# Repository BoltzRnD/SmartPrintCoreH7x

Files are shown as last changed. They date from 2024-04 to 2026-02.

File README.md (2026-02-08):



        The SmartPrintCoreH7x is an open-source 3D printer mainboard based on the STM32H7 series microcontroller.
        Copyright (C) 2024 Boltz R&D

        This Project is free Hardware: you can redistribute it and/or modify
        it under the terms of the GNU General Public License as published by
        the Free Software Foundation, either version 3 of the License, or
        (at your option) any later version.

        This Hardware is distributed in the hope that it will be useful,
        but WITHOUT ANY WARRANTY; without even the implied warranty of
        MERCHANTABILITY or FITNESS FOR A PARTICULAR PURPOSE.  See the
        GNU General Public License for more details.

        You should have received a copy of the GNU General Public License
        along with this program.  If not, see <https://www.gnu.org/licenses/>.

Contact - info@boltzrnd.com

# Contribute
I am looking for contributors and Open source organisations to maintain, expand and customize the design and sources for a voron 2.4 or similar next gen machines. being stuck in other work get me little to no time to make this project go forward for open source.

# SmartPrintCoreH7x
### Now Available to Buy from <a href="https://boltzrnd.com">Boltz R&D Store</a> , We are Shipping Globally!

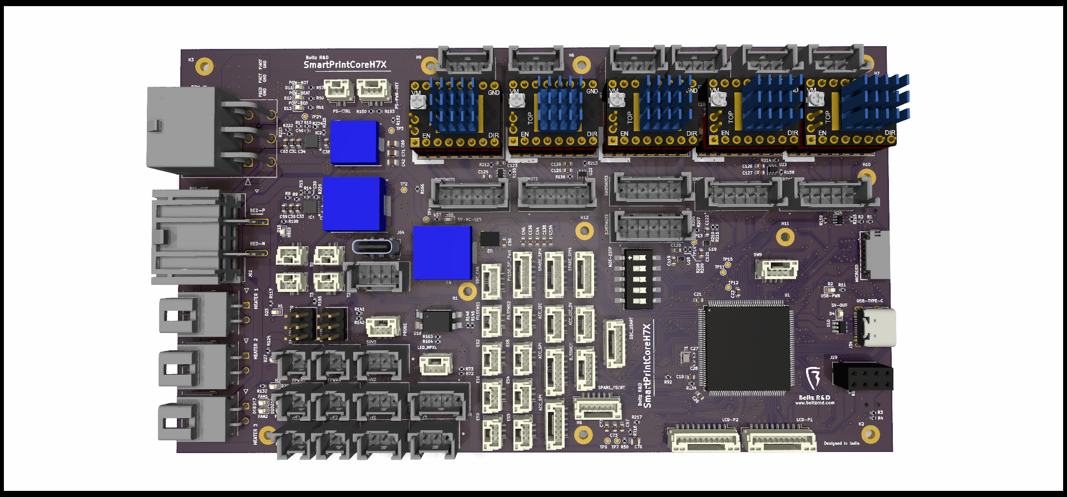
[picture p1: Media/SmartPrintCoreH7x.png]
SmartPrintCoreH7x


SmartPrintCoreH7X © 2024 by Boltz R&D is licensed under GPL V3. To view a copy of this license, visit https://www.gnu.org/licenses/gpl-3.0.en.html ---------------

The SmartPrintCoreH7x is an open-source 3D printer mainboard based on the STM32H7 series microcontroller. It includes 5+1 stepper drivers, with the option to expand by adding more sets of 5 drivers through the upcoming "SmartPrintCore Extravaganza". With a jumper-less setup and a design built for flexibility, SmartPrintCoreH7x is dedicated for makers, tinkerers, and the industry to build and customize.

The Board utilizes self-locking Molex MegaFit(Power Input), Ultra-Fit Tangless (Hotend Heaters), Mini-Lock(Motors and power peripherals) and JST-GH (Digital and IO Peripherals), for easy and worry-free connections.

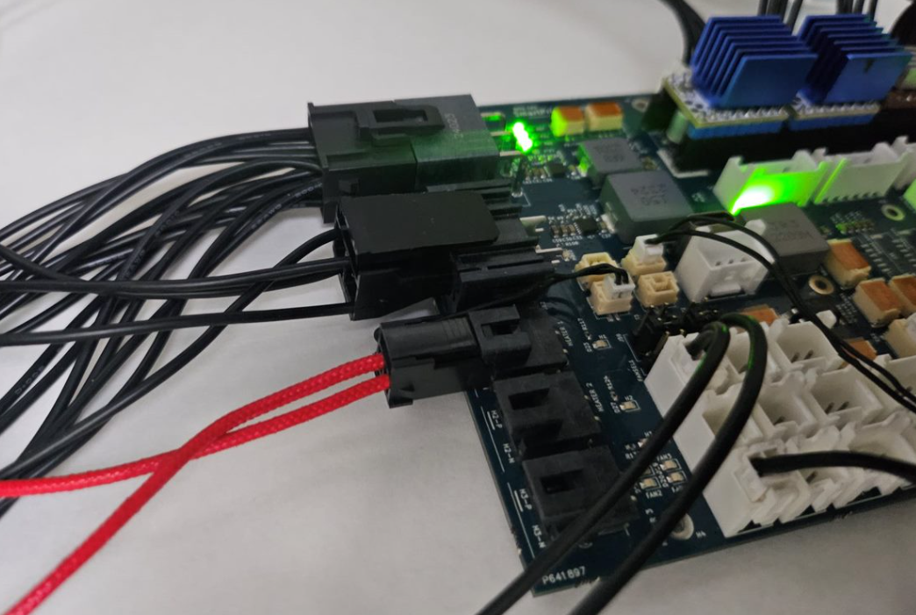
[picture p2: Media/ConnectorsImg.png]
Self-Locking Connectors Self-Locking Connectors in Action

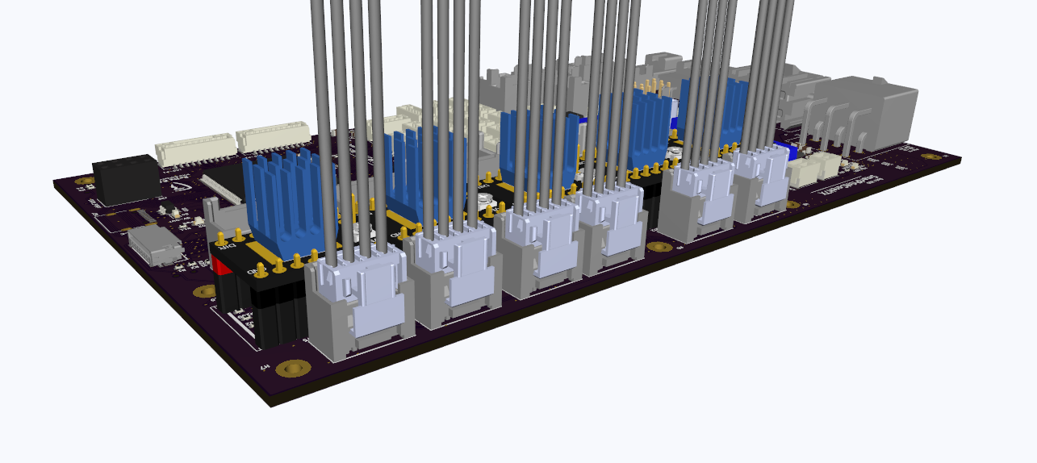
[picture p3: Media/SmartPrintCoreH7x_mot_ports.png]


The board also includes multiple TI Buck converters with more than 90% efficiencies for multiple peripherals
1. 12V 5A Fan and Peripheral Supply
2. 5V 5A Fan and Peripheral supply
3. 5V 10A SBC Supply (Optional, Can be powered by Peripheral Supply, using resistor jumpers in production)

Other notable features include -
1. Compatibility with 12V/24V power supplies
2. Auto power source selection for Board supply from USB/Main Supply.

Theraml Considerations - 
1. Low RDS(on) Mosfets are used for minimal losses, which also allows heatsink-less operation for average use cases
2. The PCB design prioritizes heat management, with strategically placed components and optimized power traces that ensure optimal cooling.

## All Features

1. Open-source design, accessible and modifiable.
2. Developed in KiCad.
3. Powered by STM32H723 MCU.
4. Supports 5+1 Stepper motors (Expandable in multiples of 5 using SmartPrintCore Extravaganza expansion board).
5. Supports dedicated five closed-loop external stepper ports.
6. USB-C with auto power switching for seamless MCU power management without setting jumpers.
10. Four PWM and two always-on fan ports (Total 6 Fan ports).
11. Dual voltage compatibility with 24V and 12V power supplies.
12. Four servo channels.
13. Single side-entry locking connector for simplified power input.
14. TI buck converters ensure efficient and reliable power supply to SBC and components.
15. Dedicated 5V supply for SBC (10A max, to support Bigger LCD and other SBC peripherals) with locking connector and Type-C port.
16. Auxiliary power: 5V 5A and 12V 5A for peripherals and fans.
17. 3.3V 1A auxiliary supply for Wi-Fi modules and small devices.
18. High-efficiency MOSFETs for cooler operation.
19. 15A heated bed with a locking connector.
20. Three high-power heaters with locking connectors.
22. Onboard slow-burning fuse for added safety.
    - Optional: External additional inline fuses for power input are recommended (included in BOM).
24. DIP switch configuration for easy sensorless homing setup.
25. Preconfigured switchable microstepping with preinstalled SMD resistors.
26. Buffered signals for motor SPI and UART.
27. Supports both Marlin and Klipper firmware.
28. Clearly marked stepper drivers for easy orientation identification and setup.

## Ports Overview

| Port Category | Quantity | Details |Recommended Rating(Operating) | Current Rating (Absolute Max Unless Notified)|
|---|---|---|---|---|
| Power Input | 1 | 6-in-1; Min: 12V, Max - 24V | 15A | 60A Total: 20A BED, 20A Motors, 20A Heaters  |
| Steppers | 5 (+1) | 2 Ports for Z Stepper | 15A | 20A |
| Smart Steppers Port | 5 (+1) | | 15A | 20A |
| Heaters | 3 | | 15A | 20A |
| Bed Heaters | 1 | | 15A | 20A |
| Accelerometer | 3 (Total) | 1 x SPI 3.3V, 1 x I2C 5V, 1 x I2C 3.3V | 0.5A | 1A |
| ESP-01 UART | 1 | | 0.5A | 1A |
| FAN | 6 | 4 x PWM + 2 x Always On, Switchable | 2A each port,4A across all ports | 5A |
| Servo | 4 | | 2A each port,4A across all ports | 5A |
| Aux Servo Power | 1 | 5V | 4A | 5A |
| SPI (Spare) | 3 | 1 x 3.3V + 2 x 5V | 0.5A | 1A 5V, 0.2A 3.3V |
| PT100 SPI Port | 1 | | 0.2A | 0.2A |
| USART | 2 | | 1A | 2A |
| SBC Supply | 2 | 1 x 4-pin Connector + 1 x Type C | 8A | 10A |
| CAN | 1 | | 0A(No Power on CAN Port) | 0A |
| Temperature Sensors | 4 | | N/A | N/A |
| Endstops | 6 | | N/A | N/A |
| Filament Sensors | 2 | | N/A | N/A |
| LCD Connector Set | 1 | | 1A | 2A |
| SWD | 1 | | N/A | N/A |
| PS CTRL | 1 | | N/A | N/A |
| PS PWR DET | 1 | | N/A | N/A |
| Neopixel LED Port | 1 | | 1A | 2A |
| BLTOUCH Port | 1 | | 1A | 2A |
| Probe | 1 | | 1A | 2A |
| MicroSD | 1 | | N/A | N/A |

## Jumpers and Configurations

| Configuration | Options | Description |
|---|---|---|
| Sensorless Homing | 1 | Configurable through onboard DIP switches |
| Fan Voltage Selection | 2 | Selectable voltages: 12V, 5V, or POWER_IN |

## Design Considerations
To optimize general usage and simplify installation, the following design features have been incorporated:

1. **External Inline Fuses**: Installed beyond the power supply line for easy fuse replacement without the need to dismantle the mainboard section of your printer.
2. **Pre-Configured Stepper Jumpers**:
   - Jumpers are preset to high using 0402 resistors, eliminating the need for manual adjustments.
   - MSX bit changes are managed via firmware if you are utilizing hardware settings.
   - Note: A4988/DRV8266 and SPI-based drivers cannot be mixed and used concurrently without soldering additional 0402 configuration resistors.

## Contribute to the SmartPrintCore Open Source Project Lineups

We are actively looking for contributors to keep this project alive, Join us in making 3D printing more accessible, reliable, and fun for everyone. Let's create, innovate, and inspire the future, one layer at a time.

Feature Requests and Bug Reports are most welcome :)

## Buy From
1. Boltz R&D - Contact us at info@boltzrnd.com or Buy Directly from https://www.boltzrnd.com
2. -- More to Come --

Interested in becoming a listed manufacturer? Reach out to us at info@boltzrnd.com to add your store link here.

## Compatible Accesories -
1. Cases -
Note - Stay tuned to our Thingiverse channel to be the first one to know - https://www.thingiverse.com/boltzrnd/designs

# Story Time

### How It Was Created
SmartPrintCoreH7x was born out of a combination of long commute hours and a renewed passion for building. With 7 hours a day of travel time, a result of embarking on an exciting single life, there was a great opportunity to reconnect with my hobby of creating innovative hardware. Fueled by endless cups of Chai Tea and free time, I found a new rhythm between the rails and circuits.

### Why It Was Created
The motivation behind SmartPrintCoreH7x is rooted in both personal need and a broader vision for the 3D printing community:
- **High-Speed Performance**: Designed to handle extremely high printing speeds of 300 mm/s or more.
- **Unmatched Control**: Providing complete control over the hardware, allowing for extensive customization and modification at any time to meet evolving needs, for any organization and individuals.
- **Reliable and Easy Connections**: To eliminate common issues with connectivity in intensive printing operations.
- **Open Source Commitment**: Ensuring the hardware remains open and accessible, allowing anyone to modify and improve upon the design without restriction.
- **Safety and Reliability**: Integrating robust power supplies to safeguard the system, particularly enhancing the performance and reliability of connected Single Board Computers (SBCs).

# Commitment to Open Source

**Note:** In celebration of our dedication to open-source hardware and software, Boltz R&D endorses the use of BeaglePlay and BeagleBone SBCs with SmartPrintCoreH7X. We are committed to actively supporting the community by ensuring seamless interfacing and integration of these setups or similar setups.

# Extra notes

1. Marlin Configuration is still under development, Please Raise a requirement on discord to prioritize it above other tasks if needed.
2. The Component Libraries are not included and redistributed because of license restrictions, contact us to join our organisation as a "contributor" to access the part libraries for development.
3. Custom 3D Printed casing is under development and evaluation, and is expected to release by end of May 2024.
4. The Klipper Configuration files are minimal, and will require some modifications to fit your use case, reach out to us whenever in doubt.
5. Feel Free to reach out to our discord server for any queries related to integration, development and production.
6. You can also send us feature requests that you'd like to see in the next versions of the board.

# Disclaimer

The SmartPrintCoreH7x is an open-source project provided by Boltz R&D. It is offered "as is" and without any warranties or guarantees, express or implied.

Boltz R&D provides no warranty of any kind regarding the safety, reliability, durability, and performance of the SmartPrintCoreH7x. By using this project's design, software, or hardware, you expressly acknowledge and agree that you assume all risks associated with its use.

Boltz R&D shall not be liable for any claims, damages, or other liabilities whatsoever, whether in an action of contract, tort or otherwise, arising from, out of, or in connection with the SmartPrintCoreH7x or the use or other dealings in this project.

This project is provided as an open-source resource for the community to use, modify, and distribute subject to the terms of the GPL V3 license. All third parties manufacturing, selling, or using the SmartPrintCoreH7x are responsible for ensuring that their products and services comply with all applicable laws and regulations.

Users are responsible for compliance with local laws, and for ensuring that appropriate safety measures are in place when manufacturing, using, or modifying the SmartPrintCoreH7x mainboard.

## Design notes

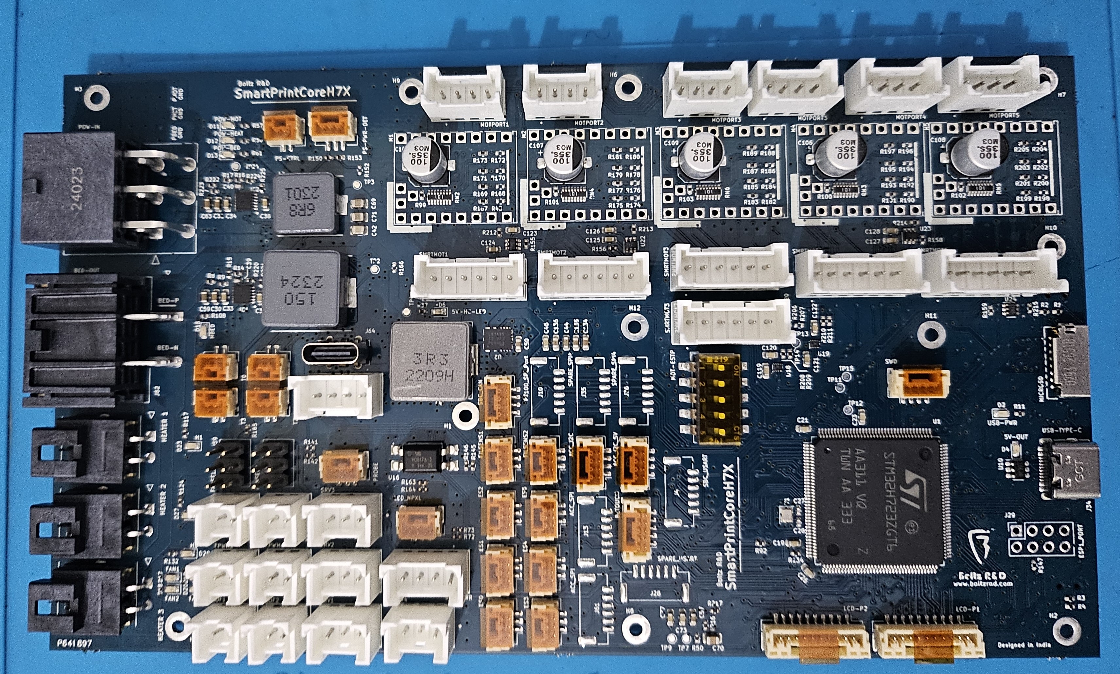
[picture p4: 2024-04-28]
Media/TheProto.jpg

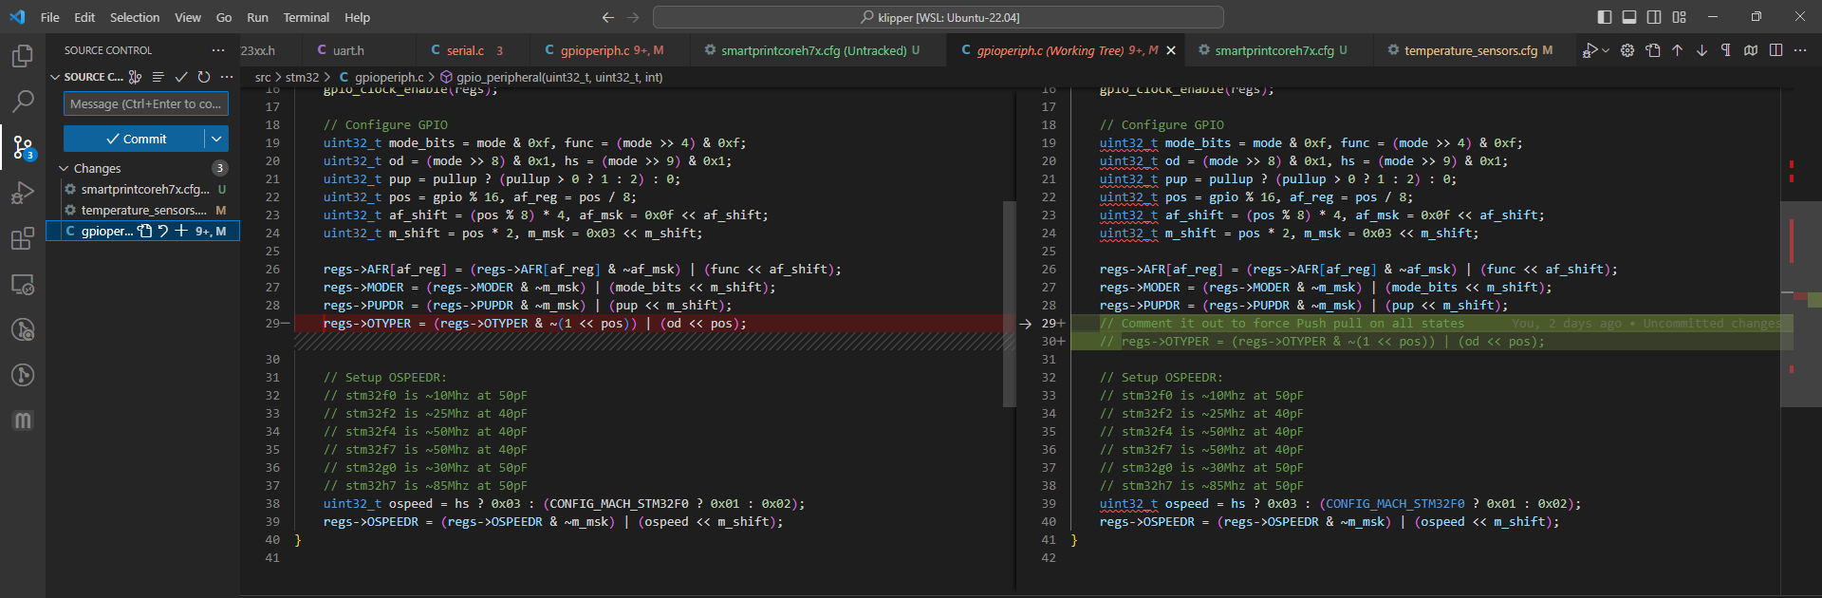
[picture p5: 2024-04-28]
FirmwareConfigs/PushPull_serial.png

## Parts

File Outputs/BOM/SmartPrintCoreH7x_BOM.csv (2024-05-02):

Reference | Value | Footprint | Manufacturer_Part_Number | Qty
C1, C3, C5, C10-C13, C15-C26, C29, C33-C35, C37, C38, C43, C45-C49, C51, C52, C58, C62, C65, C72-C83, C85, C87-C92, C94-C96, C98, C99, C101, C103, C110, C111, C115, C119-C130, C137 | 100nF | Capacitor_SMD:C_0603_1608Metric | CL10B104JB8NNNC | 78
C2, C7-C9, C14, C84, C93, C100, C102, C104 | 2.2uF | Capacitor_SMD:C_0603_1608Metric | GRM188R61E225KA12J | 10
C4, C6, C32, C36, C50, C57, C86, C116, C135, C136 | -- mixed values -- | Capacitor_SMD:C_0603_1608Metric | CL10A105KB8NNNC | 10
C27, C28 | 6pF 1% | Capacitor_SMD:C_0402_1005Metric | GCM1555C1H6R0FA16D | 2
C30, C31, C44, C59, C63, C64, C134 | 10uF 50V | Capacitor_SMD:C_0805_2012Metric | GRM21BR61H106KE43L | 7
C39, C40 | 1pF 50V | Capacitor_SMD:C_0402_1005Metric | CC0402CRNPO9BN1R0 | 2
C41, C60, C61, C66, C114 | 22uF 35V | Capacitor_SMD:C_1206_3216Metric | C3216X5R1V226M160AC | 5
C42, C69, C71, C117, C118 | 47uF 10V | Capacitor_SMD:C_0805_2012Metric | GRM21BR61A476ME15L | 5
C53-C55 | 100uF 10V | Capacitor_SMD:C_1210_3225Metric | GRM32ER61A107ME20L | 3
C56, C139-C153 | 10uF 50V | Capacitor_SMD:C_1206_3216Metric | CL31A106KBHNNNE | 16
C67, C68, C70, C97, C112 | 10uF 16V | Capacitor_SMD:C_0805_2012Metric | CL21A106KOQNNNE | 5
C105-C109 | 100uF 35V | Capacitor_SMD:CP_Elec_6.3x7.7 | EEE-1VA101XP | 5
C113 | 4.7uF | Capacitor_SMD:C_0603_1608Metric | C1608X7S1A475K080AC | 1
C131-C133 | 2.2uF 100V | Capacitor_SMD:C_1210_3225Metric | CL32B225KCJSNNE | 3
C138 | 12pF | Capacitor_SMD:C_0402_1005Metric | GRM1555C1H120GA01D | 1
D1 | CDSOT23-T24CAN | CDSOT23-T24CAN:SOT95P230X117-3N | CDSOT23-T24CAN | 1
D2, D3 | -- mixed values -- | LED_SMD:LED_0603_1608Metric | B1911UYG-20D000114U1930 | 2
D4, D6, D7, D11-D13 | -- mixed values -- | LED_SMD:LED_0603_1608Metric | B1911PG--20D000514U1930 | 6
D8-D10 | SMBJ30C | Diode_SMD:D_SMB | SMBJ30C | 3
D14, D15, D21, D22, D24-D26, D28, D34, D35 | SS14 | Diode_SMD:D_SMA | SS14 | 10
D16-D20, D23, D27, D29 | -- mixed values -- | LED_SMD:LED_0603_1608Metric | B1911UD--20D001014U1930 | 8
D30-D33 | BAV99 | Package_TO_SOT_SMD:SOT-23 | BAV99 | 4
F1-F3 | 20A SLBLW | Fuse:Fuse_1206_3216Metric | SF-1206HH20M-2 | 3
H1-H4, H6-H12, J29, M1-M5, R43, R73, R90, R141, R152, R160, R162, R164, R166, R168, R170, R172, R174, R176, R178, R180, R182, R184, R186, R188, R190, R192, R194, R196, R198, R200, R202, R204, R207, R226, TP1-TP16, TP18-TP25 | -- mixed values -- | -- mixed values -- | DNP/NC | 71
IC1, IC2 | LMR51450SDRRR | LMR51450SDRRR:SON50P300X300X80-13N-D | LMR51450SDRRR | 2
J1 | POW-IN | 0768250006:CON_768250006_MOL | 768250006 | 1
J2, J3, J5, J8, J9 | -- mixed values -- | Connector_JST:JST_GH_BM02B-GHS-TBT_1x02-1MP_P1.25mm_Vertical | BM02B-GHS-TBT | 5
J4, J10, J13, J28, J35, J36, J61 | -- mixed values -- | Connector_JST:JST_GH_BM06B-GHS-TBT_1x06-1MP_P1.25mm_Vertical | BM06B-GHS-TBT | 7
J6, J14, J65 | -- mixed values -- | 172310-3302:1723103102 | 1723103102 | 3
J7, J45, J53-J58 | -- mixed values -- | connectorslibrary:53375-0410 | 53375-0410 | 8
J11, J17, J23, J27 | -- mixed values -- | Connector_JST:JST_GH_BM04B-GHS-TBT_1x04-1MP_P1.25mm_Vertical | BM04B-GHS-TBT | 4
J12, J15, J16, J19, J21, J22, J25, J26, J30, J31, J63 | -- mixed values -- | Connector_JST:JST_GH_BM03B-GHS-TBT_1x03-1MP_P1.25mm_Vertical | BM03B-GHS-TBT | 11
J18, J24 | -- mixed values -- | Connector_JST:JST_GH_BM10B-GHS-TBT_1x10-1MP_P1.25mm_Vertical | BM10B-GHS-TBT | 2
J20 | BLTOUCH | Connector_JST:JST_GH_BM05B-GHS-TBT_1x05-1MP_P1.25mm_Vertical | BM05B-GHS-TBT | 1
J32, J33, J37-J40 | -- mixed values -- | connectorslibrary:53375-0210 | 53375-0210 | 6
J34 | USB_C_Receptacle_USB2.0 | USB_C_MOD:USB_C_Receptacle_XKB_U262-16XN-4BVC11 | USB4105-GF-A | 1
J41-J44 | -- mixed values -- | connectorslibrary:53375-0310 | 53375-0310 | 4
J46 | Micro_SD_Card_Det | microsd:473092651 | 473092651 | 1
J47-J52 | -- mixed values -- | connectorslibrary:53375-0610 | 53375-0610 | 6
J59, J60 | -- mixed values -- | Connector_PinSocket_2.54mm:PinSocket_2x03_P2.54mm_Vertical | PH2-06-UA | 2
J62 | BED-OUT | 1720430206:MOLEX_1720430206 | 1720430206 | 1
J64 | USB_C_Receptacle_PowerOnly_6P | Connector_USB:USB_C_Receptacle_GCT_USB4115-03-C | USB4115-03-C | 1
L2 | 15uH | SRP1265A-150M:INDPM135125X650N | SRP1265A-150M | 1
L3 | 6.8uH | SRP1038CC-6R8M:INDPM110100X400N | SRP1038CC-6R8M | 1
L4 | 3.3uH | SRP1265C-3R3M:IND_SRP1265C-3R3M | SRP1265C-3R3M | 1
L5 | 1uH | Inductor_SMD:L_1008_2520Metric | DFE252012F-1R0M=P2 | 1
Q1, Q3, Q5, Q6 | AO3400A | Package_TO_SOT_SMD:SOT-23-3 | AO3400A | 4
Q2, Q4, Q7, Q8 | TPH3R704PL | TPH3R704PL:TRANS_TPHR8504PL,L1Q | TPH3R704PL | 4
R1, R3 | 220R | Resistor_SMD:R_0402_1005Metric | CRGCQ0402J220R | 2
R2, R4, R6, R7, R45-R47, R50, R55, R64, R67, R70, R75, R77, R80, R83, R85, R87, R92, R99-R104, R106, R113, R115, R118, R120, R122, R125-R129, R131, R133, R144, R147-R151, R154-R159 | 10K | Resistor_SMD:R_0402_1005Metric | CRCW040210K0FKEDC | 50
R5, R72, R134, R142, R161, R163, R165, R167, R169, R171, R173, R175, R177, R179, R181, R183, R185, R187, R189, R191, R193, R195, R197, R199, R201, R203, R205, R206, R216-R219 | 0E | Resistor_SMD:R_0402_1005Metric | CRCW04020000Z0ED | 32
R8 | 2.37M 1% | Resistor_SMD:R_0402_1005Metric | CRCW04022M37FKED | 1
R9, R223 | 200K 1% | Resistor_SMD:R_0402_1005Metric | CRCW0402200KFKEDC | 2
R10, R18-R21, R26-R29, R38-R42, R49, R56, R65, R66, R68, R69, R71, R74, R76, R78, R79, R81, R82, R84, R86, R88, R145, R208-R215 | 120E | Resistor_SMD:R_0402_1005Metric | RC0402FR-07120RL | 39
R11-R13, R37, R48 | 330E | Resistor_SMD:R_0402_1005Metric | CRGCQ0402J330R | 5
R14, R16, R32, R93-R98, R136, R146, R221, R224 | 100K | Resistor_SMD:R_0402_1005Metric | CRGCQ0402J100K | 13
R15 | 7.15K | Resistor_SMD:R_0402_1005Metric | CRCW04027K15FKED | 1
R17 | 19.1K | Resistor_SMD:R_0402_1005Metric | CRCW040219K1FKEDC | 1
R22-R25, R57, R60, R61, R108-R112, R117, R124, R132 | 4.7K | Resistor_SMD:R_0402_1005Metric | CRGCQ0402J4K7 | 15
R30, R35 | 100K 1% | Resistor_SMD:R_0402_1005Metric | CRCW0402100KFKED | 2
R31 | 16.2K 1% | Resistor_SMD:R_0402_1005Metric | CRCW040216K2FKEDC | 1
R33 | 4.99K | Resistor_SMD:R_0402_1005Metric | CRCW04024K99FKEDC | 1
R34, R89 | 5.1K | Resistor_SMD:R_0402_1005Metric | RC0402FR-135K1L | 2
R36 | 24.9K 1% | Resistor_SMD:R_0402_1005Metric | CRCW040224K9FKEDC | 1
R44 | 2.2K | Resistor_SMD:R_0402_1005Metric | CRGCQ0402J2K2 | 1
R51, R52, R58, R59, R63, R137, R138, R140 | 2.37K 1% | Resistor_SMD:R_0402_1005Metric | CRCW04022K37FKED | 8
R53, R54, R62, R139 | 4.7K 0.1% | Resistor_SMD:R_0402_1005Metric | RT0402BRE074K7L | 4
R91, R143 | 1K | Resistor_SMD:R_0402_1005Metric | CRGCQ0402J1K0 | 2
R105, R107, R114, R116, R119, R121, R123, R130 | 12K | Resistor_SMD:R_0402_1005Metric | RC0402FR-1312KL | 8
R135 | 453K | Resistor_SMD:R_0402_1005Metric | CRCW0402453KFKEDC | 1
R153 | 15K 1% | Resistor_SMD:R_0402_1005Metric | RC0402FR-1015KL | 1
R220 | 46.4K | Resistor_SMD:R_0402_1005Metric | ERJ-2RKF4642X | 1
R222 | 1.21M 1% | Resistor_SMD:R_0402_1005Metric | CRCW04021M21FKED | 1
R225 | 37.4K | Resistor_SMD:R_0402_1005Metric | CRCW040237K4FKED | 1
RN1-RN6 | 100E | YC248_JR_07100RL:R_Array_Convex_8x0602 | YC248-JR-07100RL | 6
SW1, SW2 | -- mixed values -- | Button_Switch_SMD:Panasonic_EVQPUM_EVQPUD | TL1014BF160QG | 2
SW3 | MOT-ESTP | Button_Switch_SMD:SW_DIP_SPSTx05_Slide_6.7x14.26mm_W8.61mm_P2.54mm_LowProfile | 219-5LPSTR | 1
U1 | STM32H723ZGT6/STM32H743ZITx | Package_QFP:LQFP-144_20x20mm_P0.5mm | STM32H723ZGT6 | 1
U2 | LM61495RPHR | LM61495RPHR:RPH0016A | LM61495RPHR | 1
U3 | TXS0108ERGYR | txs0108gyr:IC_TXS0108ERGYR | TXS0108ERGYR | 1
U4 | CD74HCT365M | cd4504:SOIC127P600X175-16N | CD74HCT365M | 1
U5 | SN74LVC8T245RHLR | SN74LVC8T245RHLR:IC_SN74LVC8T245RHLR | SN74LVC8T245RHLR | 1
U8 | LP5912-3.3DRV | lp5912-3.3vdrvrmod:WSON-6-1EP_2x2mm_P0.65mm_EP1x1.6mm_ThermalVias | LP5912-3.3DRV | 1
U9 | TJA1051TK-3 | Package_DFN_QFN:DFN-8-1EP_3x3mm_P0.65mm_EP1.55x2.4mm | TJA1051TK-3 | 1
U10 | USBLC6-2SC6 | Package_TO_SOT_SMD:SOT-23-6 | USBLC6-2SC6 | 1
U11 | W25Q128JVS | Package_SO:SOIC-8_5.23x5.23mm_P1.27mm | W25Q128JVS | 1
U12 | CD40109BPWR | Package_SO:TSSOP-16_4.4x5mm_P0.65mm | CD40109BPWR | 1
U15 | TLV62568DRL | Package_TO_SOT_SMD:SOT-563 | TLV62568DRL | 1
U16 | VO617A-3X007T | VO617A-3X007T:SOIC254P1016X440-4N | VO617A-3X007T | 1
U17 | L78L10_SOT89 | Package_TO_SOT_SMD:SOT-89-3 | L78L10ACUTR | 1
U18, U19 | TXS0102DQE | txs0102_mod:X2SON-8_1.4x1mm_P0.35mm | TXS0102DQE | 2
U20, U22-U24 | TXS0101DCK | Package_TO_SOT_SMD:SOT-363_SC-70-6 | TXS0101DCK | 4
U21 | TPS2116DRLR | Package_TO_SOT_SMD:SOT-583-8 | TPS2116DRLR | 1
Y1 | NX2016SA-25MHZ-EXS00A-CS11321 | Crystal:Crystal_SMD_2016-4Pin_2.0x1.6mm | NX2016SA-25MHZ-EXS00A-CS11321 | 1

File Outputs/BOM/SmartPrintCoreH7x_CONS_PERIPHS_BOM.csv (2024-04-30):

Connectors References | Description | Manufacturer_Part_Number | Qty | Pins MPN | Per Conn Pins Qty | Total Pins Qty | Wire(AWG) | Wire Length(mm) | Wire MPN | Wire Qty (mm)
J1 |  | 171692-0206 | 1 | 768230345 | 6 | 6 | 10 | 100 |  | 600
J2, J3, J5, J8, J9 |  | GHR-02V-S | 5 | SSHL-002T-P0.2 | 2 | 10 | 28 | 80 |  | 800
J4, J10, J13, J28, J35, J36, J61 |  | GHR-06V-S | 7 | SSHL-002T-P0.2 | 6 | 42 | 28 | 80 |  | 3360
J6, J14, J65 |  | 172256-3102 | 3 | 1722537023 | 2 | 6 | 18 | 100 |  | 600
J7, J45, J53-J58 |  | 511630400 | 8 | 507528200 | 4 | 32 | 20 | 100 |  | 3200
J11, J17, J23, J27 |  | GHR-04V-S | 4 | SSHL-002T-P0.2 | 4 | 16 | 28 | 80 |  | 1280
J12, J15, J16, J19, J21, J22, J25, J26, J30, J31, J63 |  | GHR-03V-S | 11 | SSHL-002T-P0.2 | 3 | 33 | 28 | 80 |  | 2640
J18, J24 |  | GHR-10V-S | 2 | SSHL-002T-P0.2 | 10 | 20 | 28 | 80 |  | 1600
J20 |  | GHR-05V-S | 1 | SSHL-002T-P0.2 | 5 | 5 | 28 | 80 |  | 400
J32, J33, J37-J40 |  | 511630200 | 6 | 507528200 | 2 | 12 | 20 | 100 |  | 1200
J41-J44 |  | 511630300 | 4 | 507528200 | 3 | 12 | 20 | 100 |  | 1200
J47-J52 |  | 511630600 | 6 | 507528200 | 6 | 36 | 20 | 100 |  | 3600
J62 |  | 172672-2002 | 1 | 1718250100 | 2 | 2 | 11 | 100 |  | 200
MOT1-MOT5 | Motor Headers | PPPC081LFBN-RC | 10
JMPRS1, JMPRS2 | FANSEL Jumpers | QPC02SXGN-RC | 2
FANSEL1-FANSEL2 |  | 861400062YO2LF | 2
FuseHolder1-FuseHolder3 | In Line with +Vin Pins of J1 | 01530002H | 3 |  |  |  | 10 | 50
Fuse |  | 0297015.WXNV | 3
HEATSINK1-HEATSINK7 | For MOSFETs and Bucks | XSD57-067 | 7

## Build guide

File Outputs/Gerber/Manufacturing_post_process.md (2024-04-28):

# The Manufacturing Post-processing requires the following steps
1. Layering a Minimum of 0.3mm of Solder on exposed Tracks of Bed Power Connector.
2. Assembly of Connectors.
3. Adding Jumpers for Fan Sel 1 and 2.
4. In Line Fuses for Each power input line for Motor, Bed and Heaters.
5. Installation of Heatsinks on Buck Converters, and Heater Mosfets if required.
6. Installation of Casing with Fan if required.

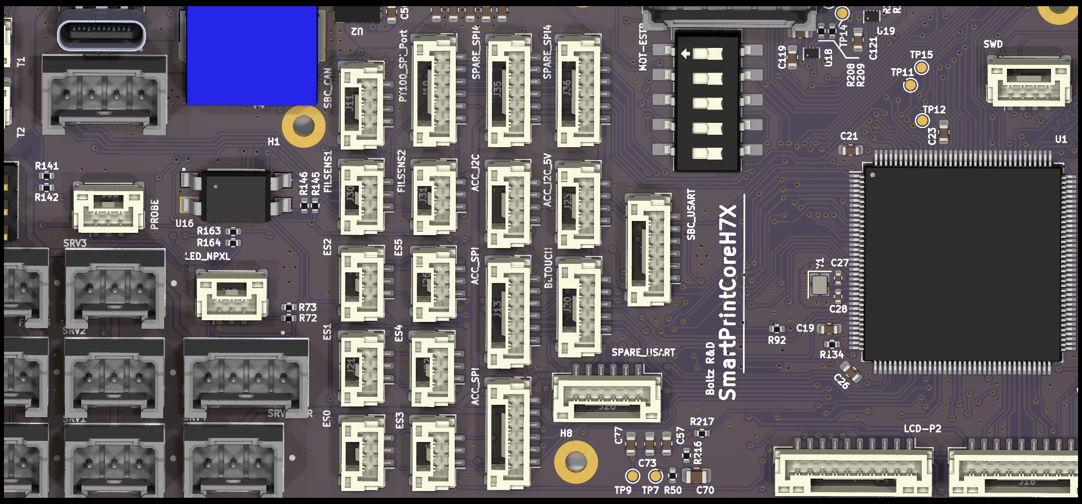
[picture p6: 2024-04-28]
Media/SmartPrintCoreH5x_periph_ports.png

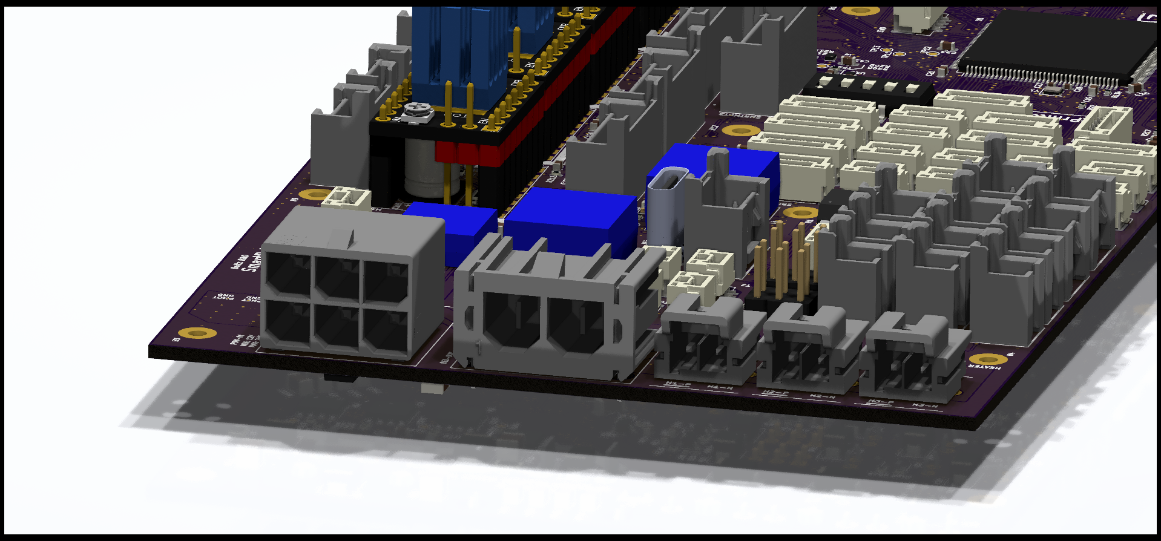
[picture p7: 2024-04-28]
Media/SmartPrintCoreH7x_heater_ports.png

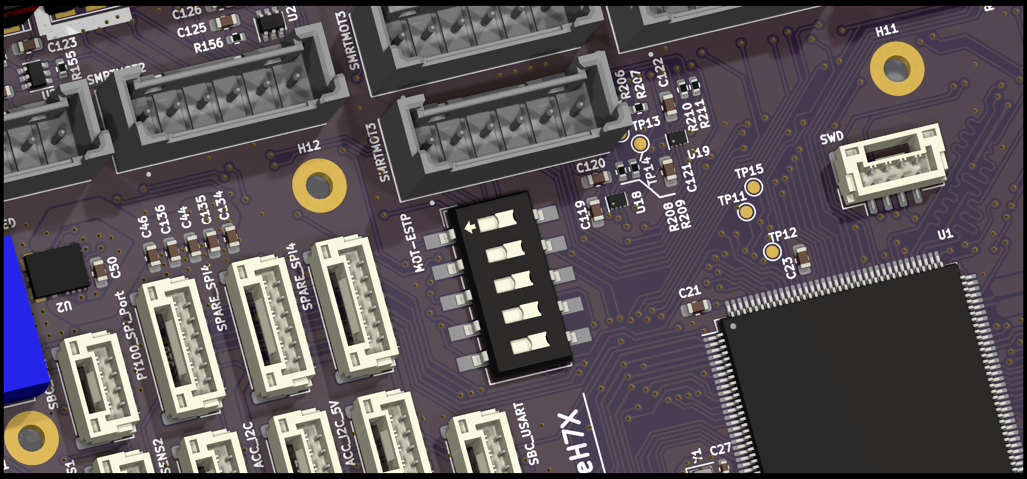
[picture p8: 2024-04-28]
Media/SmartPrintCoreH5x_mot_estp_sw.png

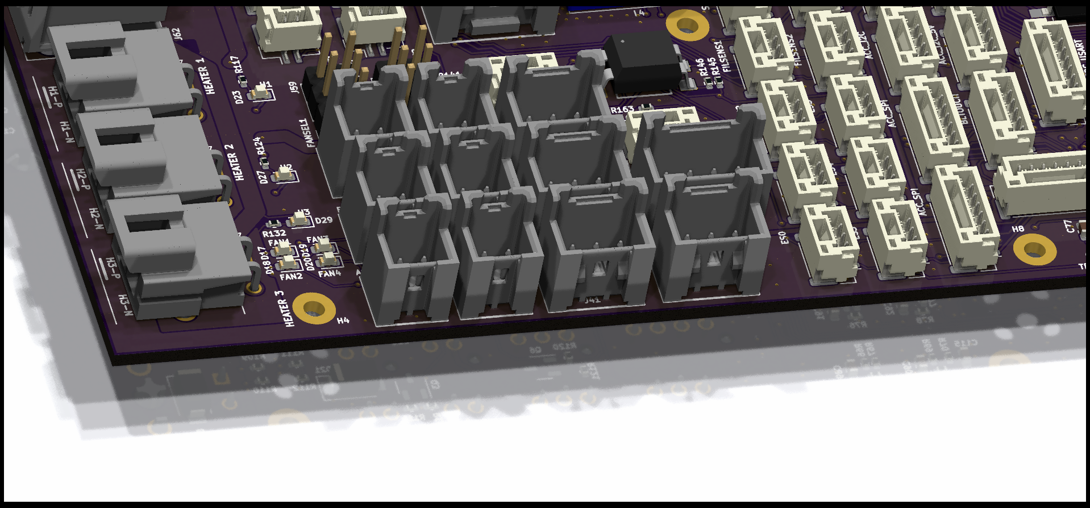
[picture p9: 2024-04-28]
Media/SmartPrintCoreH5x_fan_ports.png

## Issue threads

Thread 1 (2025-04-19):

R8 resistor values are different in schamatics and board

galmiklos, 2025-04-19:
The value of R8 is 237k in the board, while it is shown 2.37M in the schematics. Looks like the BOM was created from the schematics, because it is 2.37M in the BOM, too.

After reading the datasheet of the LMR51450SDRRR, if my calculations are correct, a value of 237k would mean the "12V 5A Buck" DC-DC converter would require a minimum of 3.059V (typical 2.73V) input voltage from the "heat" power supply, which sounds too little, so I am guessing the "correct" value would be 2.37M, which would mean a minimum of 17.99V (typical 16.06V). Although, it sounds a bit too high to me. It is stated elsewhere that the power supply voltage range is 12V-24V, but of course, although it is a low dropout converter, you cannot really have a 12V DC-DC converter supplied from 12V. I suppose the correct values in the statement should be "18V-24V".

Yatin-Khurana, 2025-04-22:
Hello @galmiklos, I've verified the calculations, You are correct, the value will be 2.37M for the resistor so that It'll only turn on after 18V minimum, the idea is that if the user is powering the machine but 12V, they generally don't need the 12V buck to be active (and the voltage difference would be too little for the buck to work reliably), because they can use the HEAT supply or any other power input also, even for the fans user can switch the jumpers to power from POW_HEAT directly to get 12V.

In conclusion, the bug reported was correct. I'll fix the design files and documentation for the same.
I'll keep this issue open till the fix is merged.

Thank you for reporting the issue.

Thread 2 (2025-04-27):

LCD ports don't match any known LCD module PIN mapping

galmiklos, 2025-04-27:
The way the PINs of ports J18 and J24 are assigned functions to, do not match any known LCD module PIN mapping, if used by straight 1 to 1 flat ribbon cable between the board side GHR-10V-S connectors, and the LCD side 2x5 IDC pin headers. It is of course possible to make a cable by separating the wires in the ribbon cable and criss-cross them as needed, but that's not ideal.

Yatin-Khurana, 2025-04-29:
Thanks for highlighting the issue Miklos,

P.S - issue will be fixed in next revision

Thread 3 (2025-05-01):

Reset is missing from SWD connector

galmiklos, 2025-05-01:
It's more of an inconvenience. J-Link from SEGGER (maybe other debuggers too) can handle reset, and ideally the reset line of the MCU is connected to a pin on the J-Link debugger. (Please, see SWD Connector Pinout at https://www.segger.com/products/debug-probes/j-link/technology/interface-description/). But there is no reset line in the SWD connector (J27). It could be a 5 pin connector with reset in the next revision.

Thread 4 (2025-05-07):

Main voltage is too low before switching over to USB power

galmiklos, 2025-05-07:
With the values of R6 (10k) and R7 (10k) providing a voltage split to PR1of U21 (TPS2116) , 5V_HC has to drop to about 2V, before U21 switches over to VBUS_IN. This is too low for the MCU, and so it is restarted every time when main power is plugged/unplugged, while the USB is connected. With values of R7=4.7k and R6=12k the "cutoff" voltage would be about 3,5V. I tested it, and it seems to work.

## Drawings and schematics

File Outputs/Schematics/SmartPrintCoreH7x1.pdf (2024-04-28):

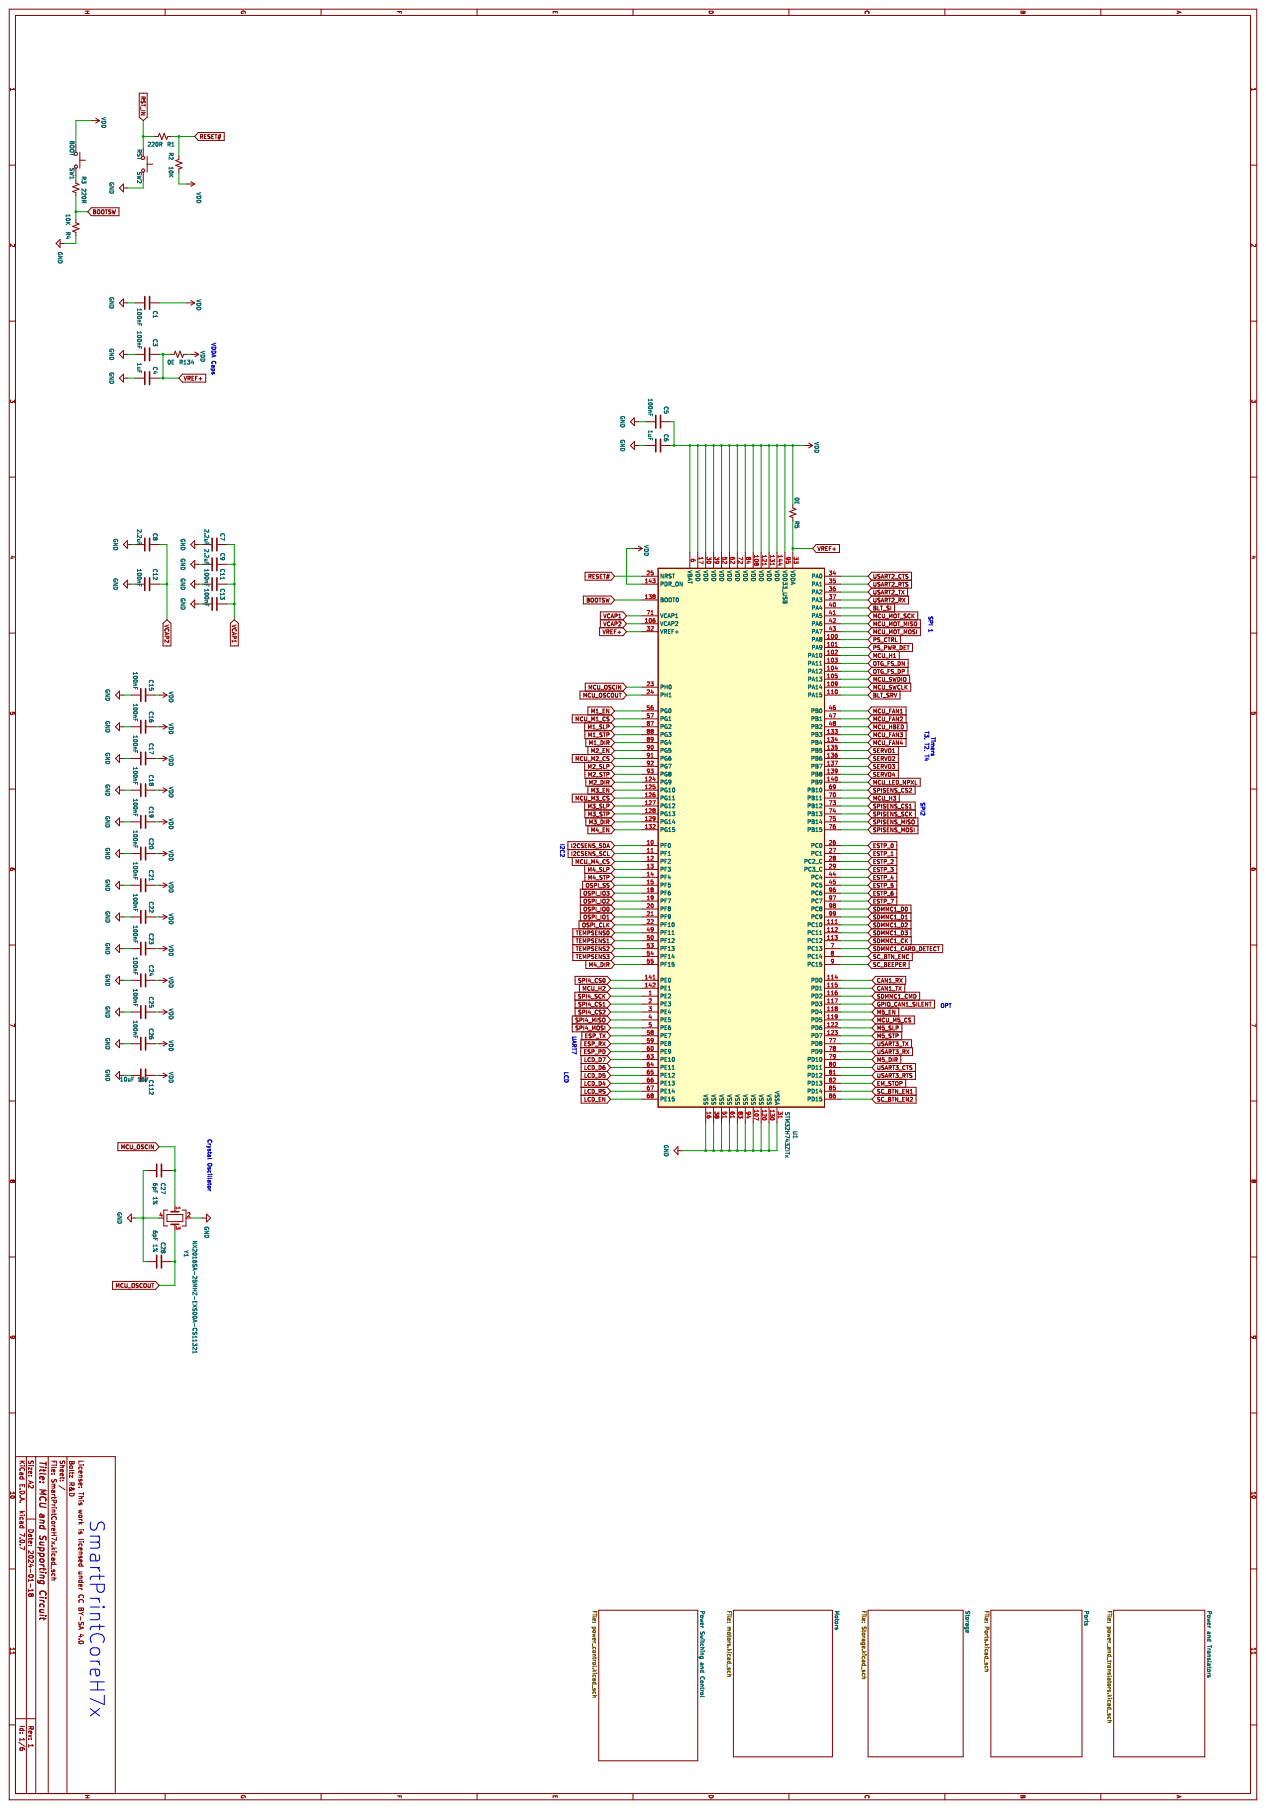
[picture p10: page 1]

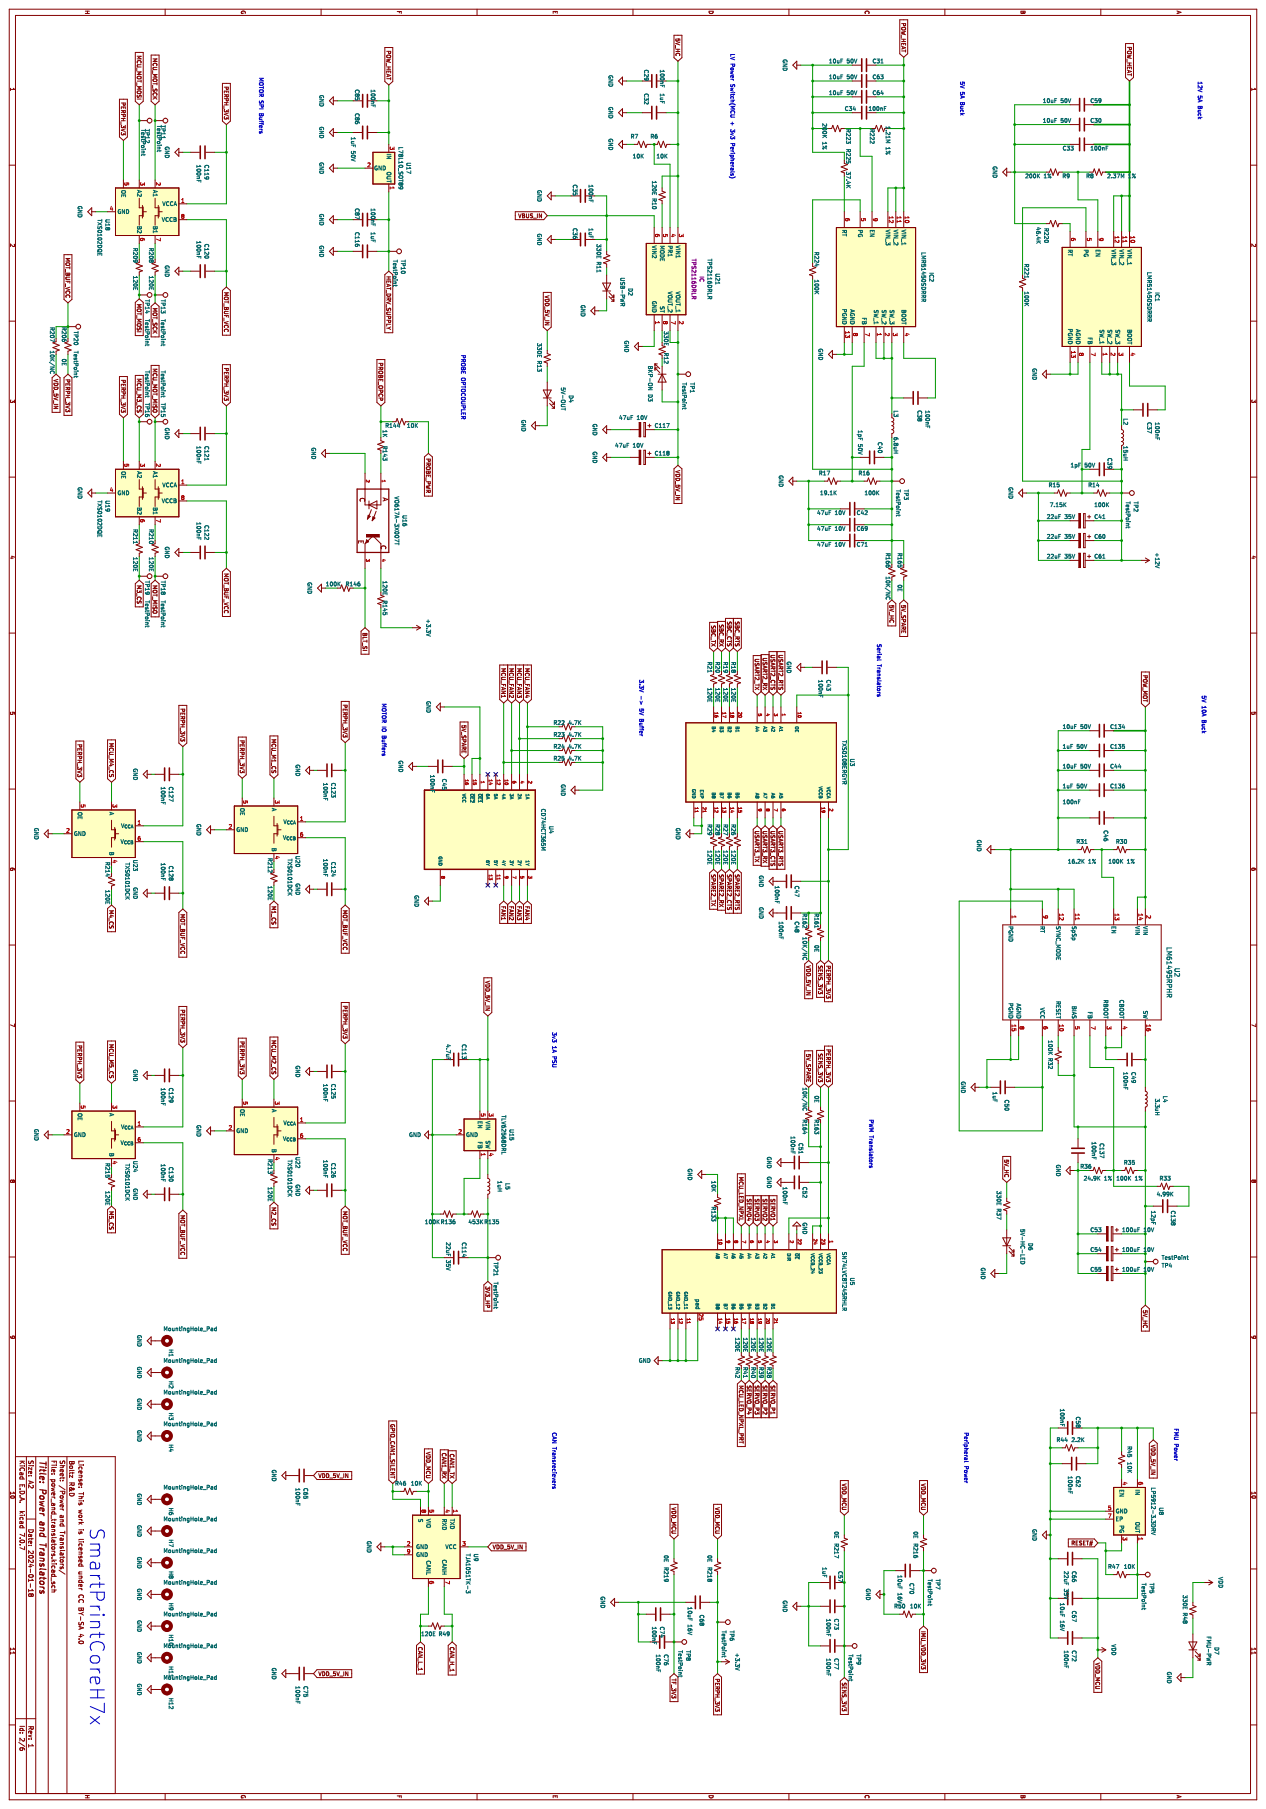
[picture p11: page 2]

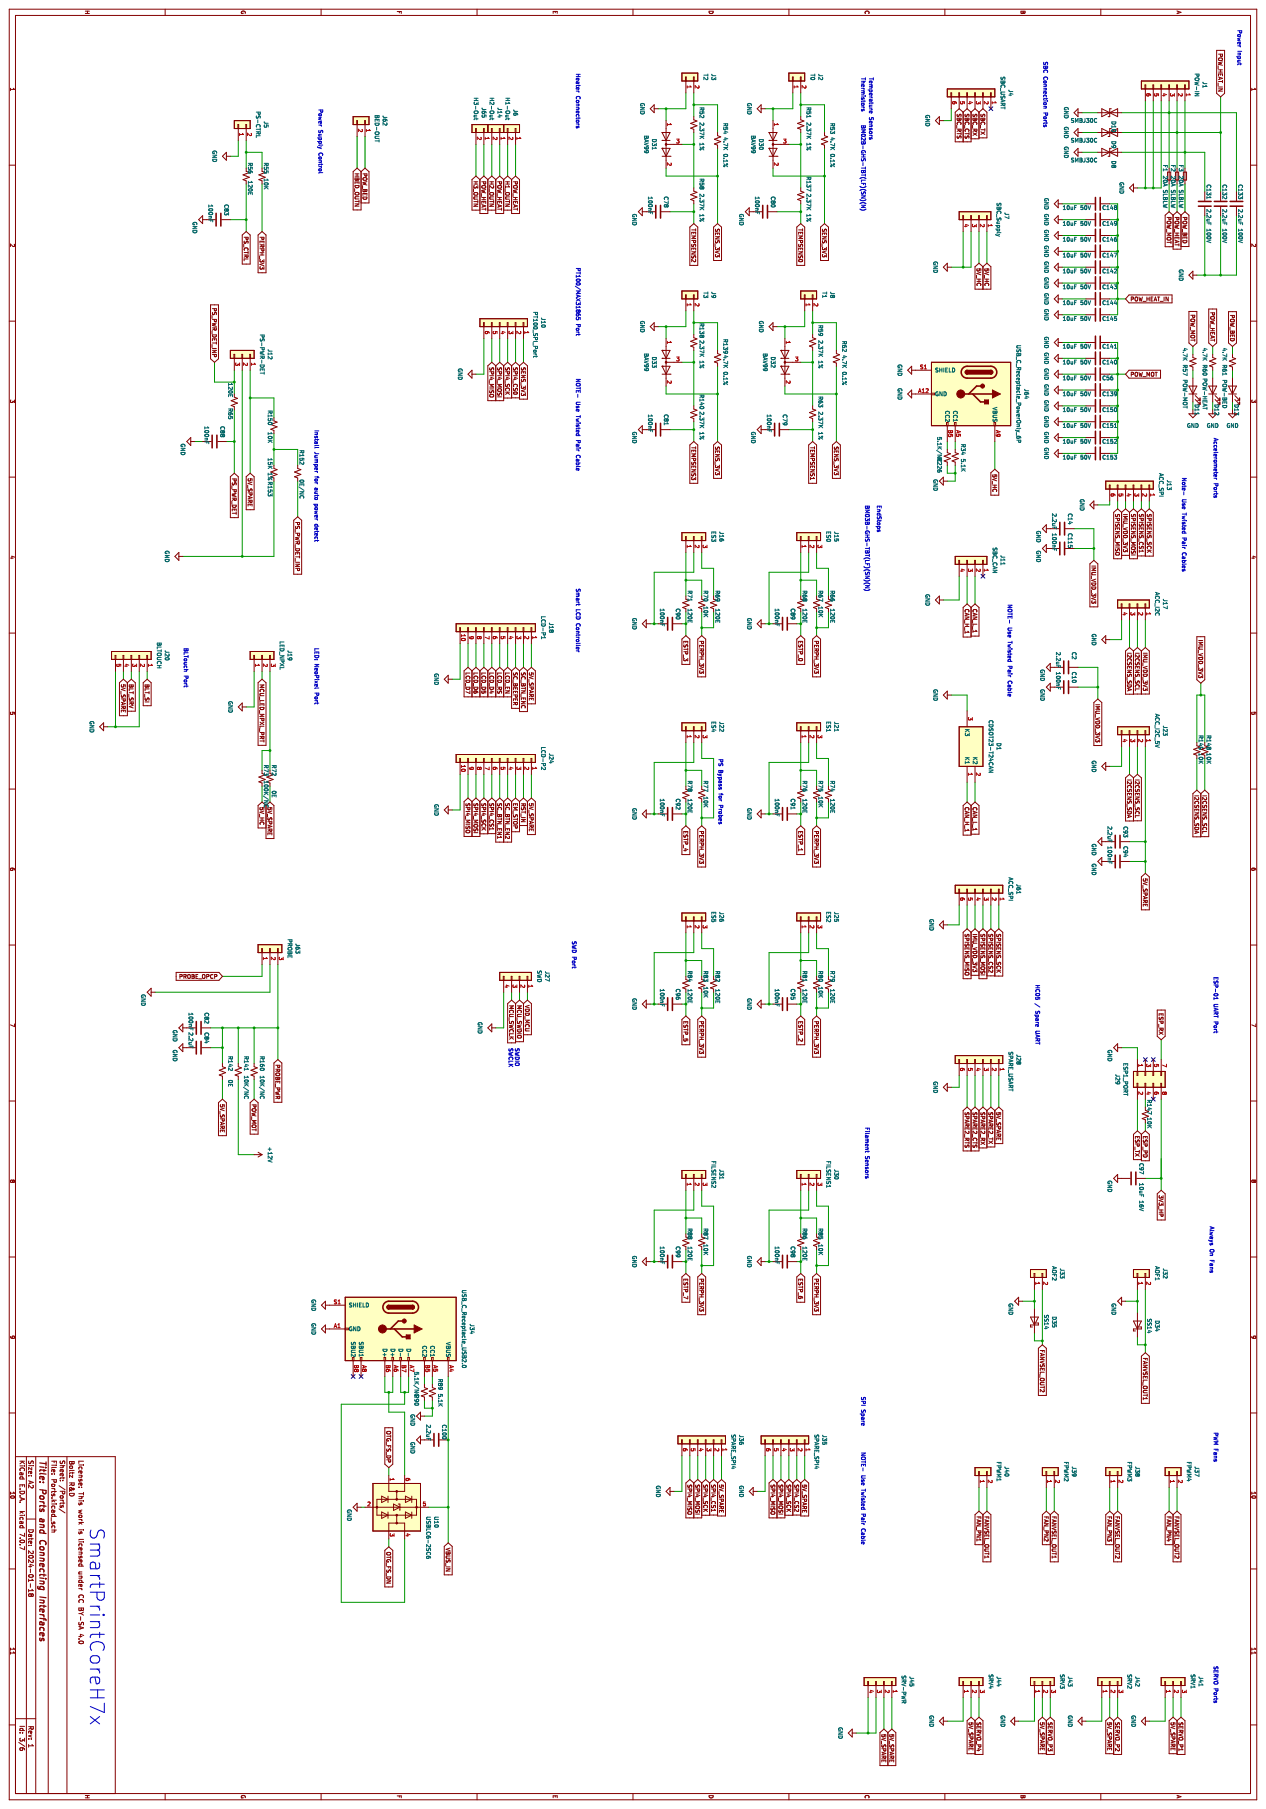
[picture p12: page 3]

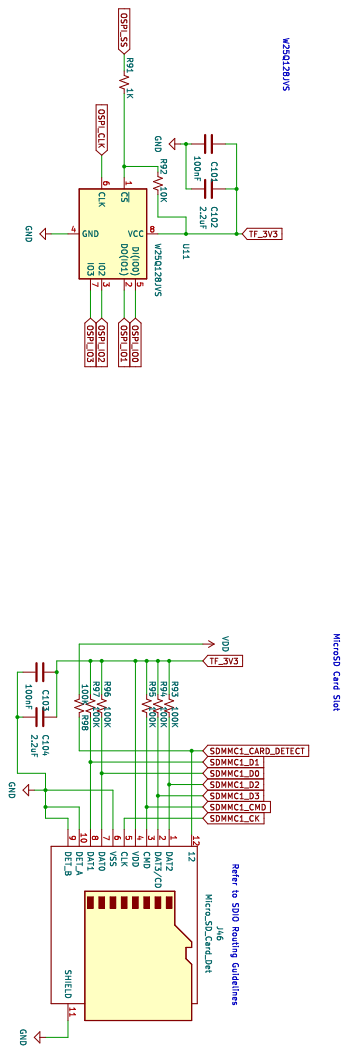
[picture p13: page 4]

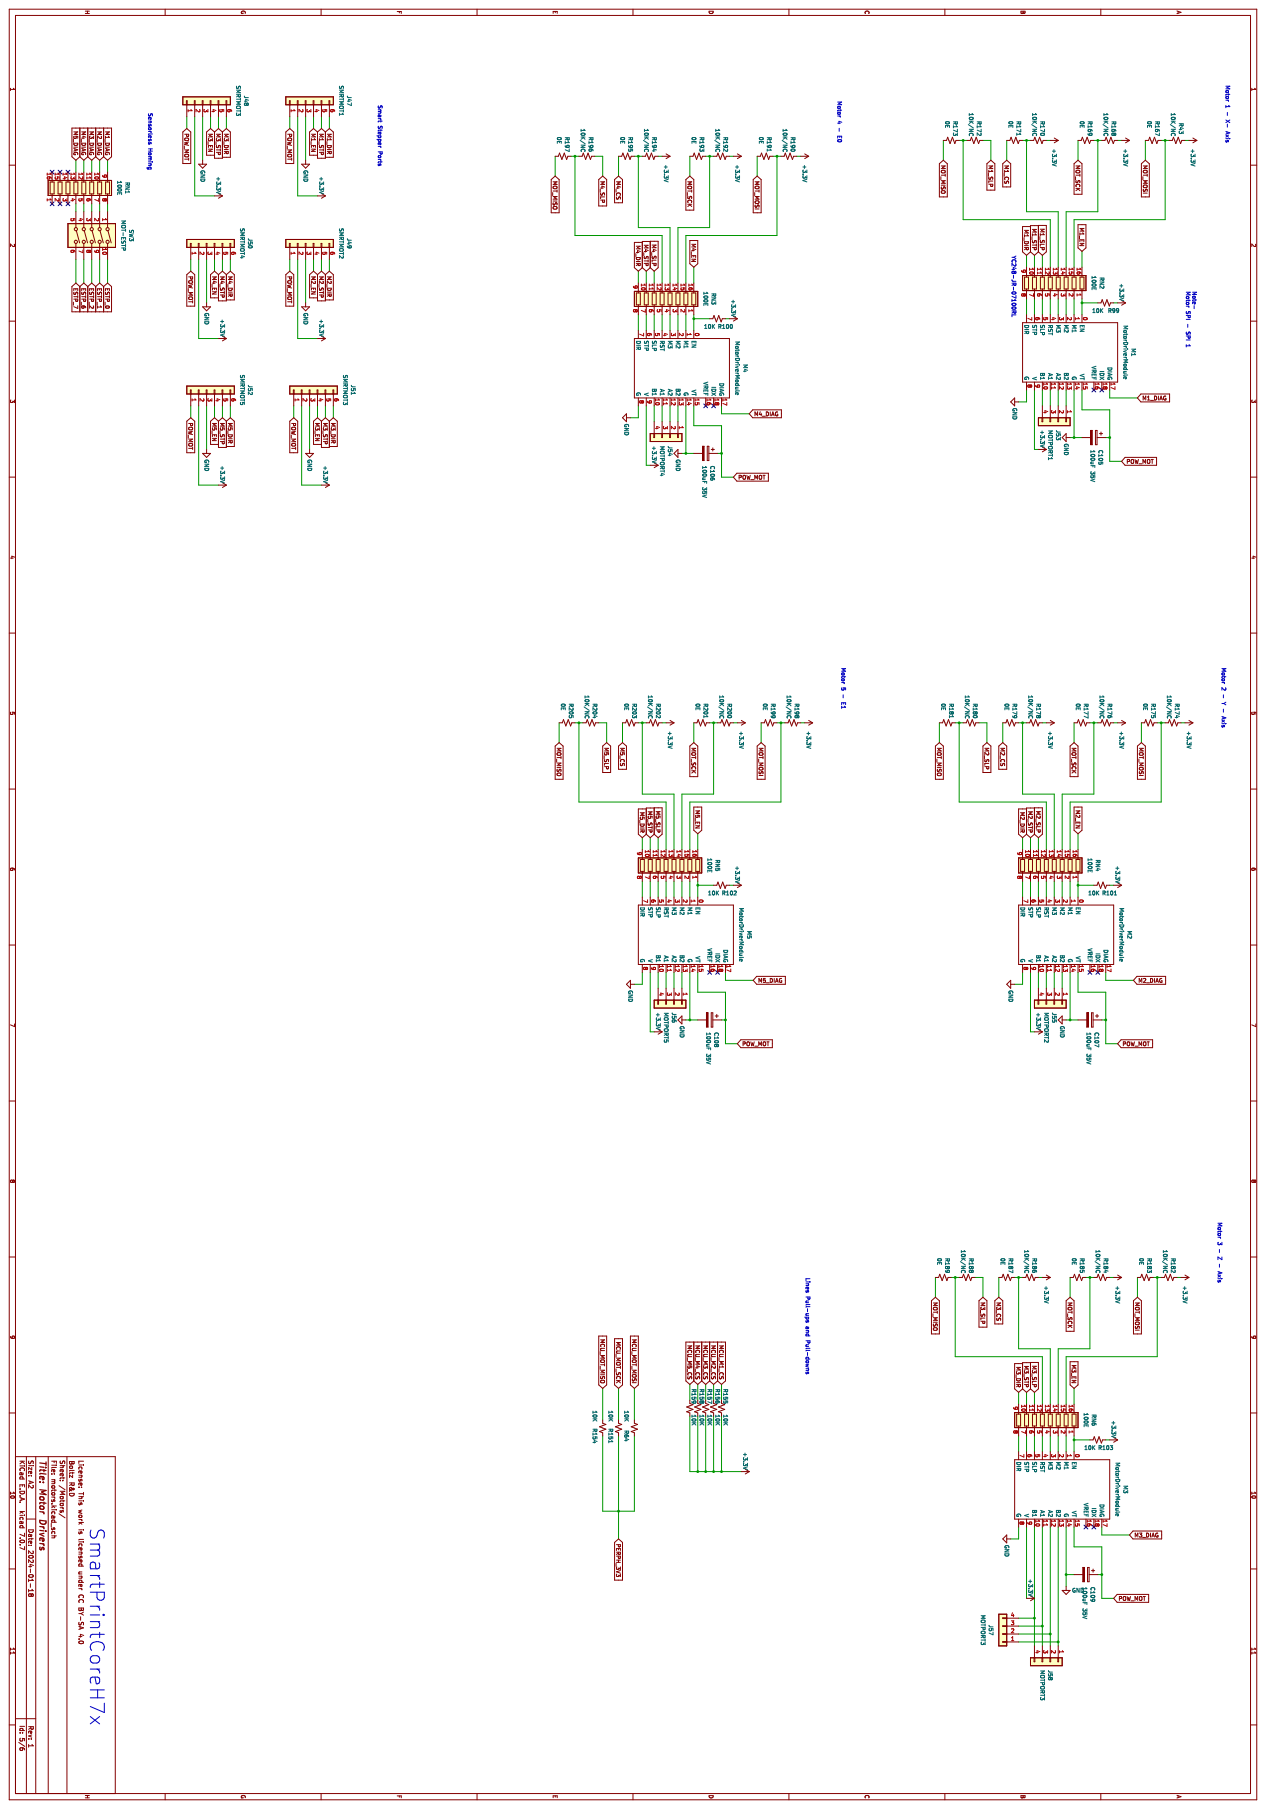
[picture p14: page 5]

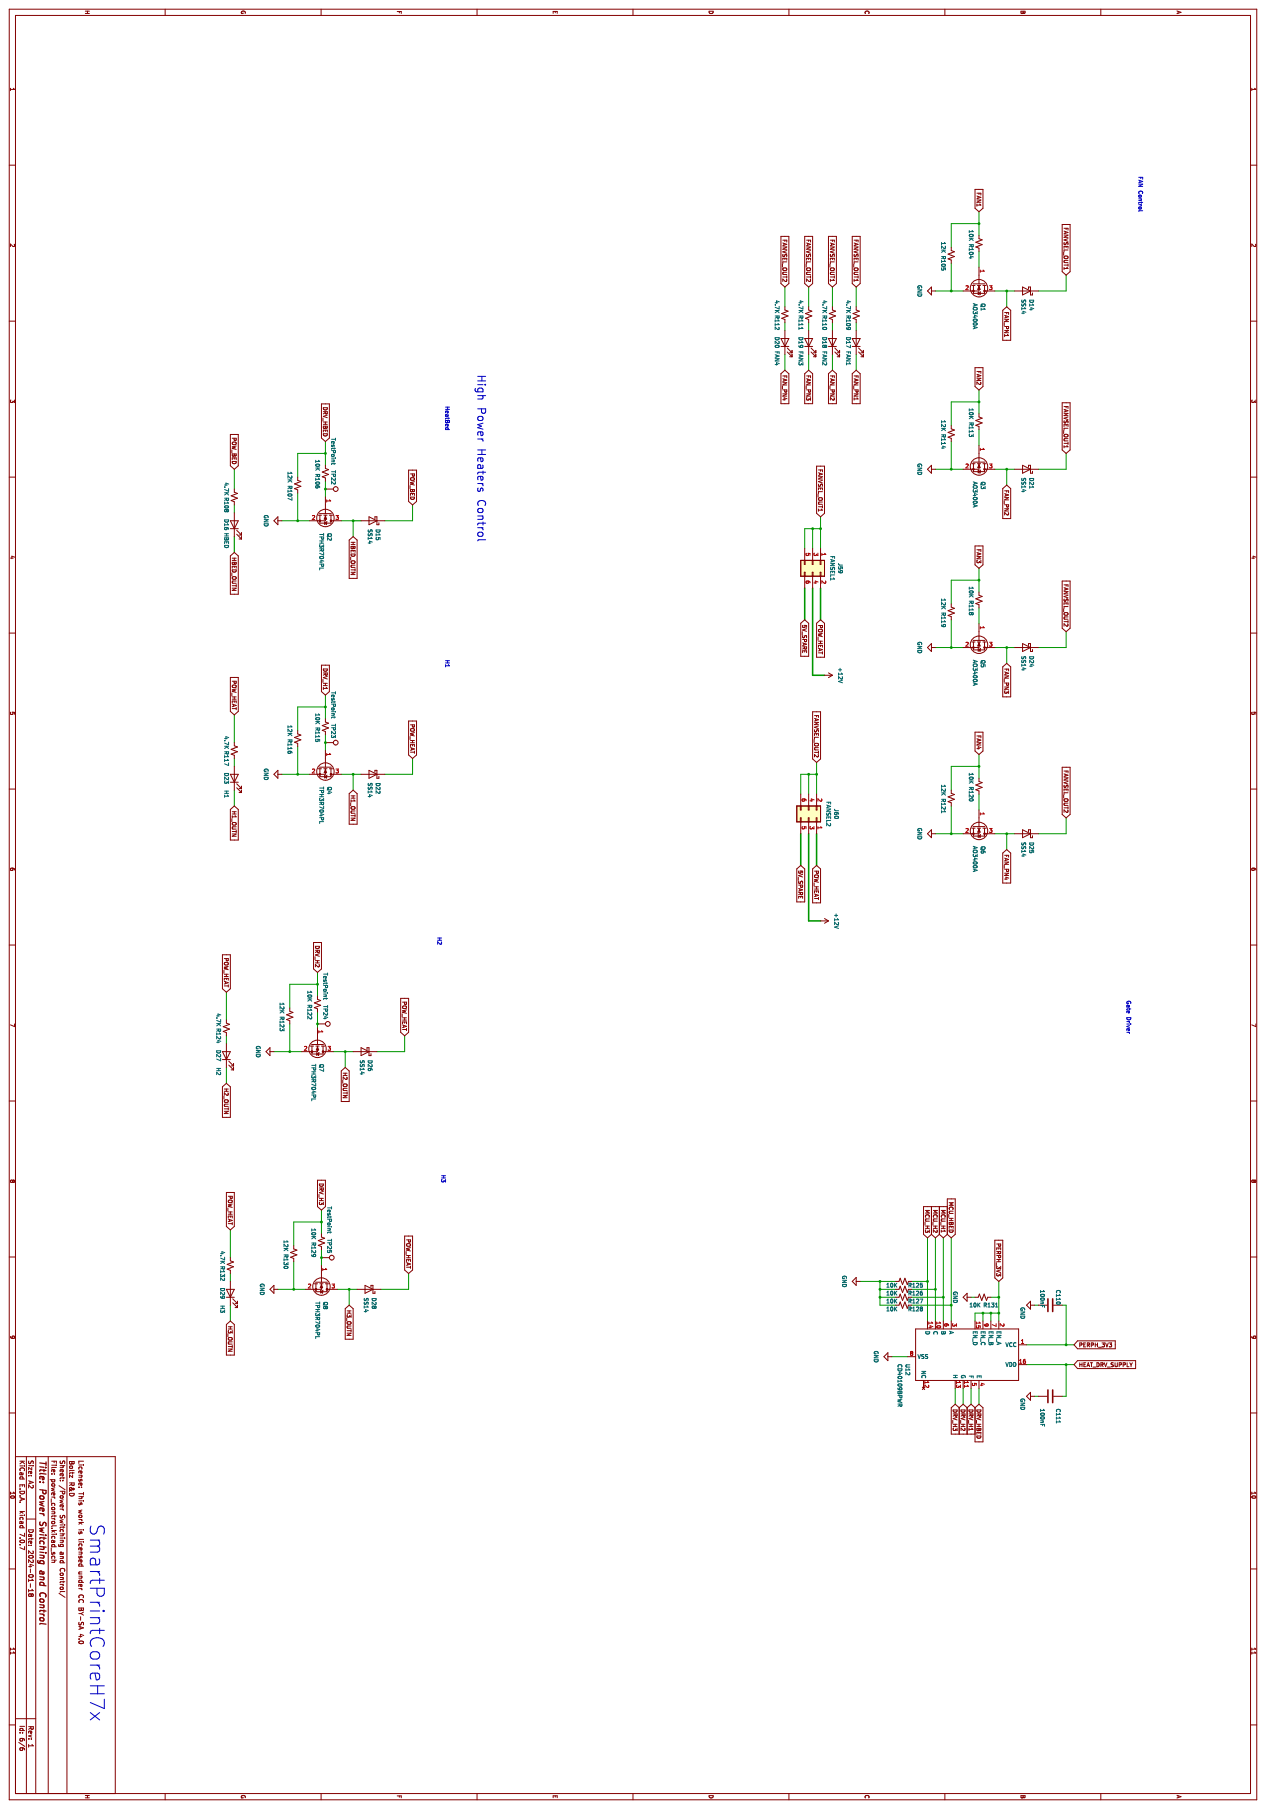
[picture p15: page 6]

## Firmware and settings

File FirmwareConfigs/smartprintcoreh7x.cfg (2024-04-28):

[include fluidd.cfg]
[include mainsail.cfg]
[virtual_sdcard]
path: /home/debian/printer_data/gcodes
on_error_gcode: CANCEL_PRINT

# Note - this is a draft example for the configuration, modify the file based on your usage or
# message us at info@boltzrnd.com for a custom Config file based on your machine.

# This file contains common pin mappings for the Boltz R&D SmartPrintCoreH7x.
# To use this config, the firmware should be compiled for the
# STM32H723 with a "no Bootloader" "25 MHz crystal"
# and "USB (on PA11/PA12)" or "CAN bus (on PD0/PD1)" or "USART2 PA3/PA2" at 115200 Baud.
# note if using Serial UART modify the code as given in "PushPull_serial.png" to force push pull on GPIO.

# See docs/Config_Reference.md for a description of parameters.

# Motor-1
[stepper_x]
step_pin: PG3
dir_pin: PG4
enable_pin: !PG0
microsteps: 256
rotation_distance: 40
endstop_pin: ^!PC0
position_endstop: 0
position_max: 200
homing_speed: 50

# Motor-2
[stepper_y]
step_pin: PG8
dir_pin: PG9
enable_pin: !PG5
microsteps: 256
rotation_distance: 40
endstop_pin: ^!PC3
position_endstop: 0
position_max: 200
homing_speed: 50

# Motor-3
[stepper_z]
step_pin: PG13
dir_pin: !PG14
enable_pin: !PG10
microsteps: 16
rotation_distance: 2
endstop_pin: ^!PC2
position_endstop: 0.0
position_max: 200

# Motor-4
[extruder]
step_pin: PF4
dir_pin: !PF15
enable_pin: !PG15
microsteps: 16
rotation_distance: 33.500
nozzle_diameter: 0.400
filament_diameter: 1.750
pullup_resistor: 4700
heater_pin: PA10
sensor_pin:  PF12
sensor_type: EPCOS 100K B57560G104F
control: pid
pid_Kp: 22.2
pid_Ki: 1.08
pid_Kd: 114
min_temp: 0
max_temp: 250

#[filament_switch_sensor material_0]
#switch_pin: PC6

#[filament_switch_sensor material_1]
#switch_pin: PC7

# Motor-5
[extruder1]
step_pin: PD7
dir_pin: !PD10
enable_pin: !PD4
microsteps: 16
rotation_distance: 33.500
nozzle_diameter: 0.400
filament_diameter: 1.750
pullup_resistor: 4700
heater_pin: PE1
sensor_pin:  PF13
sensor_type: EPCOS 100K B57560G104F
control: pid
pid_Kp: 22.2
pid_Ki: 1.08
pid_Kd: 114
min_temp: 0
max_temp: 250

[heater_bed]
heater_pin: PB2
sensor_pin: PF11
sensor_type: EPCOS 100K B57560G104F
control: pid
pid_Kp: 22.2
pid_Ki: 1.08
pid_Kd: 114
min_temp: -200
max_temp: 300

[heater_fan hotend_fan]
pin: PB0

[fan]
pin: PB3

[heater_fan controller_fan]
pin: PB1

[temperature_fan chamber]
pin: PB4
max_power: 1.0
shutdown_speed: 0.0
cycle_time: 0.0005     #2 kHz PWM signal
hardware_pwm: False
kick_start_time: 0
sensor_type: NTC10K
sensor_pin: PF14
min_temp: 0
max_temp: 70
target_temp: 0
max_speed: 0.7
min_speed: 0.1
control: pid
pid_Kp: 2.0     ;40
pid_Ki: 5.0     ;0.2
pid_Kd: 0.5     ;0.1
pid_deriv_time: 2.0
gcode_id: C

[mcu]
restart_method: command
serial: /dev/ttyS0
baud: 115200

[printer]
kinematics: cartesian
max_velocity: 200
max_accel: 1000
max_z_velocity: 4
max_z_accel: 1

########################################
# TMC2209 configuration
########################################


[tmc2208 stepper_x]
uart_pin: ^PG1
#diag_pin: PC0
run_current: 0.2
stealthchop_threshold: 999999
#driver_SGTHRS: 255

[tmc2208 stepper_y]
uart_pin: ^PG6
#diag_pin: PC1
run_current: 0.2
stealthchop_threshold: 999999

#[tmc2208 stepper_z]
#uart_pin: ^PG11
##diag_pin: PC2
#run_current: 0.2
#stealthchop_threshold: 999999

#[tmc2208 extruder]
#uart_pin: ^PF2
##diag_pin: PC6
#run_current: 0.2
#stealthchop_threshold: 999999

#[tmc2209 extruder1]
#uart_pin: PD5
##diag_pin: PC7
#run_current: 0.550
#stealthchop_threshold: 999999
#uart_address: 4

########################################
# TMC2130 configuration
########################################

#[tmc2130 stepper_x]
#cs_pin: PG1
#spi_bus: spi1
##diag1_pin: PF0
#run_current: 0.800
#stealthchop_threshold: 999999

#[tmc2130 stepper_y]
#cs_pin: PG6
#spi_bus: spi1
##diag1_pin: PF2
#run_current: 0.800
#stealthchop_threshold: 999999

#[tmc2130 stepper_z]
#cs_pin: PG11
#spi_bus: spi1
##diag1_pin: PF4
#run_current: 0.650
#stealthchop_threshold: 999999

#[tmc2130 extruder]
#cs_pin: PF2
#spi_bus: spi1
#run_current: 0.800
#stealthchop_threshold: 999999

#[tmc2130 extruder1]
#cs_pin: PD5
#spi_bus: spi1
#run_current: 0.800
#stealthchop_threshold: 999999

[board_pins]
aliases:
    # FPC header, Aliases EXP1 & EXP2 for mini12864
    EXP1_1=PC14, EXP1_2=PC15,
    EXP1_3=PE15, EXP1_4=PE14,
    EXP1_5=PE13, EXP1_6=PE12,
    EXP1_7=PE11, EXP1_8=PE10,
    EXP1_9=<GND>, EXP1_10=<5V>,

    # EXP2 header
    EXP2_1=PE5, EXP2_2=PE6,
    EXP2_3=PE2, EXP2_4=PE3,
    EXP2_5=PD14, EXP2_6=PD15,
    EXP2_7=PD13, EXP2_8=<RST>,
    EXP2_9=<GND>, EXP2_10=<NC>

# See the sample-lcd.cfg file for definitions of common LCD displays.

#[bltouch]
#sensor_pin: ^PA4
#control_pin: PA15

# Proximity switch
#[probe]
#pin: PA4

#[output_pin ps_on_pin]
#pin: PA8

#[neopixel my_neopixel_1]
#pin: PB9

#[adxl345]
#cs_pin: PB12
#spi_bus: spi2

[servo servo1]
pin: PB5
initial_angle: 0

[servo servo2]
pin: PB6
initial_angle: 0

[servo servo3]
pin: PB7
initial_angle: 0

[servo servo4]
pin: PB8
initial_angle: 0

# NeoPixel Config
# https://github.com/julianschill/klipper-led_effect
[neopixel panel_ring]
pin:                     PB9
chain_count:             10
color_order: GRB
initial_RED: 0.1
initial_GREEN: 0.6
initial_BLUE: 0.2

[led_effect panel_idle]
autostart:              true
frame_rate:             24
leds:
    neopixel:panel_ring
layers:
  breathing  10 1 top (.5,.5,1)


# For Endstop-less Operation
#[homing_override]
#set_position_x: 0
#set_position_y: 0
#set_position_z: 0
#gcode:

# Set config bits if you are using A4988/DRV8266
[static_digital_output a4988_configs_z]
pins: PA5, PA6, PG11, PA7, PG12, PF2, PF3, PD5, PD6

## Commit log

2024-04-30 Updated ReadMe and Added BOMs
    [SmartPrintCoreH7x_BOM.csv, SmartPrintCoreH7x_CONS_PERIPHS_BOM.csv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]
2024-05-02 MCU MPN Corrections and Readme update
    Corrected MCU MPN to STM32H723ZGT6 (Note - user can choose from any variant compatible with STM32H723ZGT6 footprint and pin layout)
    [SmartPrintCoreH7x.kicad_sch, SmartPrintCoreH7x_BOM.csv]
